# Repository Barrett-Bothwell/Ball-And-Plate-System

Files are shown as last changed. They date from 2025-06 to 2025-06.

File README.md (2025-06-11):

# Ball and Plate Control System

Watch the demo video (https://www.youtube.com/watch?v=V8rTU_FPlsE)

*Click the image above to watch a demo of the system in action!*

A dynamic balancing system that uses an **ESP32-C3 Super Mini**, **MG995 servos**, and a **resistive touchscreen** to control the position of a ball on a plate. The system implements **modern control theory** for real-time position stabilization and uses **6302view** for visualization and debugging.
By Barrett Bothwell and Kolby Kriegelstein

---

## Features

- Real-time ball position control using state-space or observer-based feedback
- Circular pattern sert point option
- Input via resistive touchscreen for ball position sensing
- Output actuation using MG995 servos
- Visualization with **6302view**
- Built on the ESP32-C3 Super Mini platform

---

## Components Used

| Component | Description |
|---|---|
| ESP32-C3 Super Mini | Microcontroller for control and I/O |
| MG995 Servos (x2) | Control pitch and roll of the plate |
| M2x65mm Linkage Rod | Linkage Rod used to connect the plate to the servo motors |
| M2 Metal Clevis | Clevis used to connect the rod to the servo and top plate |
| Universal Joint Coupler | 10mm inner diameter universal joint |
| 7/8" Stainless Steel Ball | Ideal ball size for system and plate |
| 4-Wire Resistive Touchscreen | Senses ball position (165mm by 100mm)  
| 6302view | PC-based visualization & tuning tool |
| 5v Power Supply | Stable 5V source for servos and ESP32 |

---

## Wiring Setup

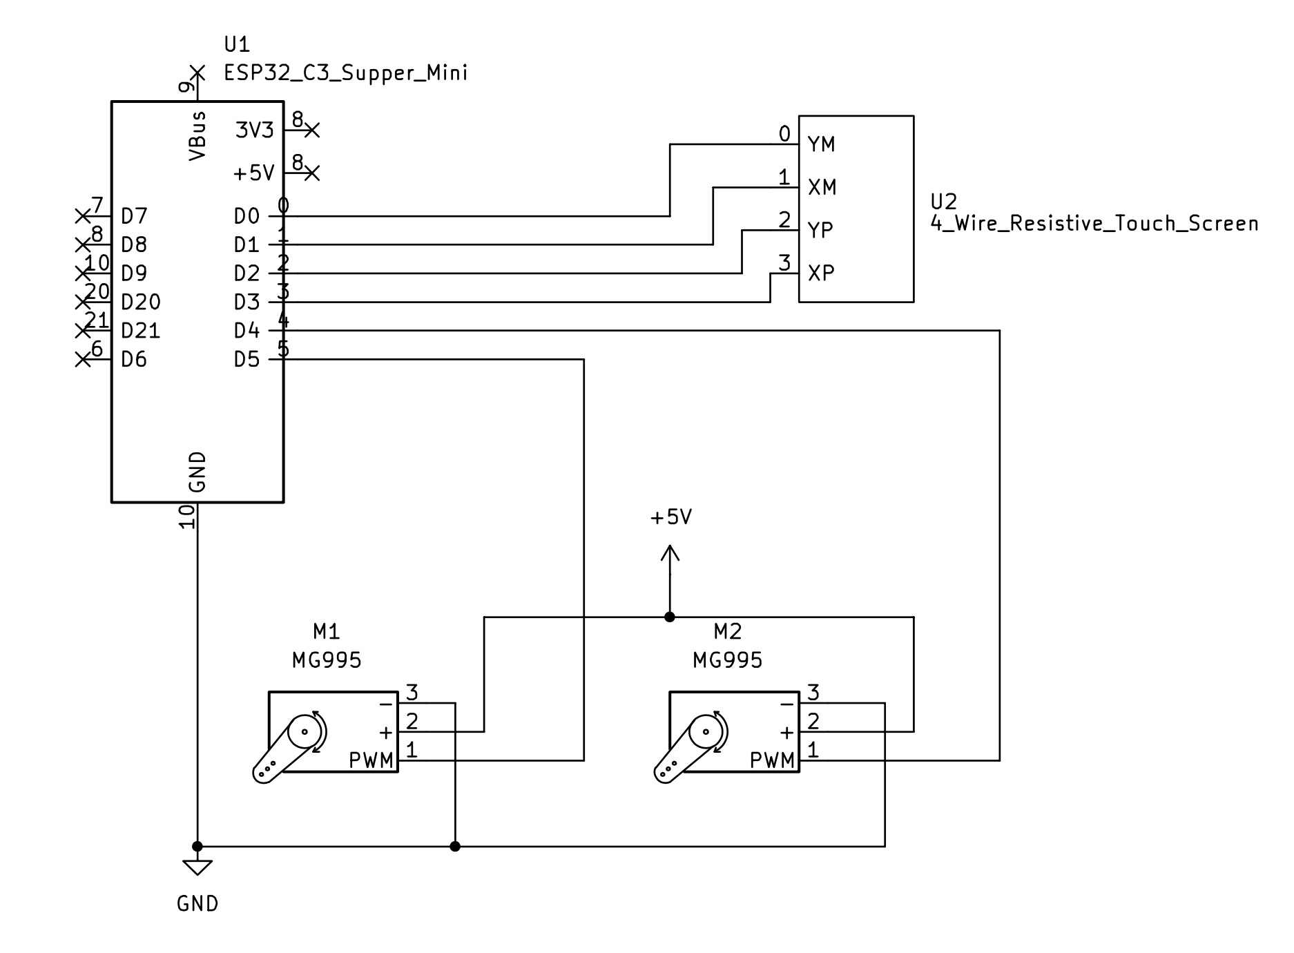
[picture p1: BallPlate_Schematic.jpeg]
Ball and Plate Schematic


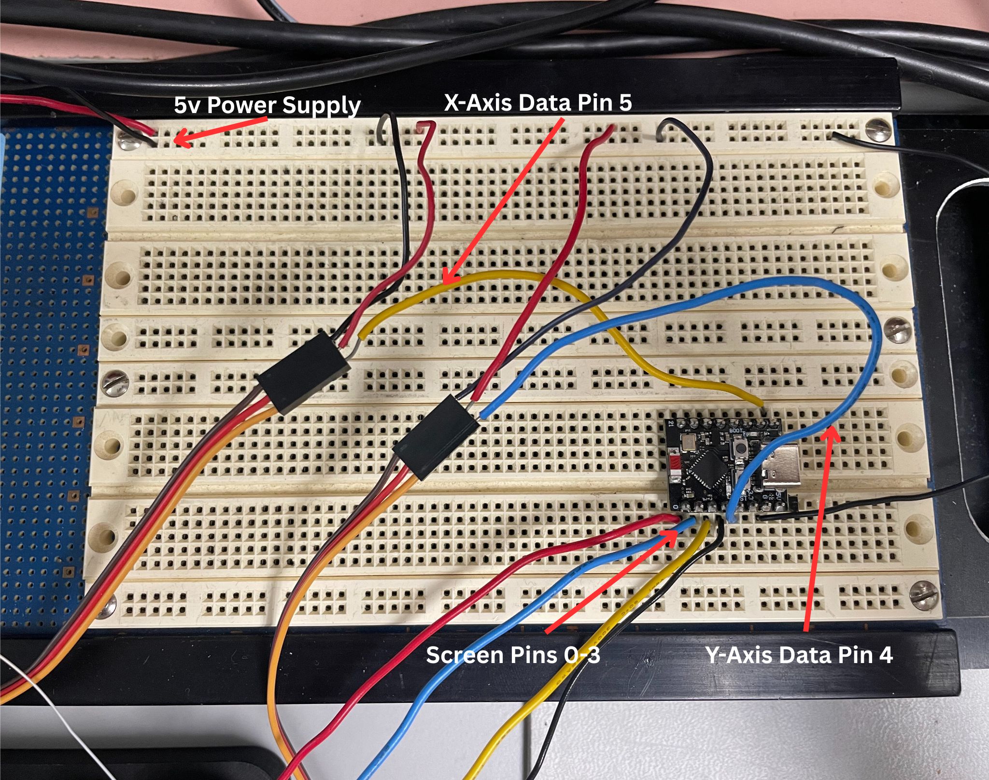
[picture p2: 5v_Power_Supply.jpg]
Wiring Diagram


| ESP32-C3 Pin | Connection |
| --- | --- |
| 5V | Servo power supply, can use external power supply |
| GND | Common ground for all components |
| Pin 5 | Servo X PWM signal |
| Pin 4 | Servo Y PWM signal |
| Pin 0 | Touchscreen X+ (analog read) |
| Pin 2 | Touchscreen X- (output control)  |
| Pin 3 | Touchscreen Y+ (output control)  |
| Pin 1 | Touchscreen Y- (analog read) |

---

## Setup Instructions

Follow these steps to set up the Ball and Plate Control System:

1. **Hardware Assembly**:
   - Start by 3D printing the top tray and bottom base
   - Once printed mount the motors by screwing them into the two posts
   - Connect the top tray and bottom base together using the universal joint
   - Finally use the metal clevises and linkage rods to connect the motors to the top tray
   - Wire the components as per the wiring diagram provided in the **Wiring Setup** section.

2. **Software Setup**:
   - Install the required development environment for the ESP32-C3 (e.g., [PlatformIO](https://platformio.org/) or Arduino IDE).
   - Open the project in your development environment and upload the firmware to the ESP32-C3.

3. **6302view Setup**:
   - Download and install **6302view** from its [GitHub repository](https://github.com/almonds0166/6302view).
   - Connect the ESP32-C3 to your PC via USB or Wi-Fi.
   - Run **6302view** and configure the serial or Wi-Fi connection to the ESP32-C3.
   - Use the offset sliders in **6302view** to level the plate if necessary.

5. **Testing**:
   - Power on the system and ensure all components are functioning correctly.
   - Use **6302view** to monitor the ball position and adjust the control parameters as needed.

---

## 6302view Integration

- **Purpose**: Enables real-time monitoring and set point placement of the system over serial communication.

- **Visualized Parameters**:
  - Current ball position (X, Y)
  - Currently commented out servo command plots
  - Target/reference position slider
  - Axis Offset sliders to account for uneven surfaces
  - Circle toggle to target a circular pattern for the ball

---

## Control Theory

This project uses a **state-space feedback controller** designed using modern control theory. The first step in finding our state space model was deriving the equation using Newton's Laws.

**Deriving the Equations of Motion Using Newton's Laws**:

The first step in designing the control system is to derive the equations of motion for the Ball and Plate system. This is done using Newton's Second Law:
\
F = ma and M = Iα

#### Assumptions:
- The ball rolls without slipping on the plate.
- The plate's motion is limited to small angular displacements (linearization assumption).
- Constant gravitational force acts on the ball.
- No additional rotation on the ball.
- No unwanted movement in the plate.

#### Steps:
1. **Free Body Diagram**:
   - Consider the forces acting on the ball:
     - Gravitational force \(mg\) acting downward.
     - Normal force \(N\) from the plate.
     - Frictional force \(F<sub>f</sub>\) preventing slipping.

2. **Equations of Motion**:
   - For the ball in the x-direction:
     \
     F<sub>f</sub> - w sin(θ) = -ma
     
   - For the rotation of the ball:
   \
    F<sub>f</sub>R = Iα 

3. **Combine Equations**:
   - Substitute the torque equation into the force equations to eliminate F<sub>f</sub>.
   \
    R(w sin(θ) - ma) = Iα

4. **Simplify**:
   - By plugging in the moment of inertia for a solid sphere:
   \
    I = 2/5mR^2
   
   - With additional algebraic simplification and a small angle approximation of sin we get:
   \
   a = 5/7gθ

This equation describes the behavior of the ball for both the respective x and y accelerations in terms of the plate angle θ. These equations will now be used to construct the state-space representation of the system.

**State Space Representation**

The state-space representation of a system is given by:
\
$\dot{x}$ = Ax + Bu

y = Cx + Du

Where:
- \( x \) is the **state vector** (e.g., ball position and velocity).
- \( u \) is the **input vector** (e.g., plate angles).
- \( y \) is the **output vector** (e.g., ball position and velocity).
- \( A, B, C, D \) are the system matrices.

#### Steps:

1. Define the States
For the Ball and Plate system, the states can be defined as:
- x = Ball position in the x-direction
- $\dot{x}$  = Ball velocity in the x-direction
- y = Ball position in the y-direction
- $\dot{y}$ = Ball velocity in the y-direction

2. Inputs and Outputs
- **Inputs \( u \)**: Plate angles in the x and y directions

- **Outputs (\( y \))**: Ball positions in the x and y directions

3. Derive the State Equations
Using the linearized equations of motion:
\[
a<sub>x</sub> =  5/7gθₓ, a<sub>y</sub> = 5/7gθᵧ
\]
We can write the second-order equations for the ball’s motion:
\[
$\dot{x}$ = 5/7gθₓ, $\dot{y}$ = 5/7gθᵧ
\]

4. Write in Matrix Form
Combine the equations into matrix form to find the final state space model:

\
$\dot{x}$ = Ax + Bu
\
y = Cx + Du

Where:

A = \
    [ 0 ,  1 ,  0 ,  0 ]\
    [ 0 ,  0 ,  0 ,  0 ]\
    [ 0 ,  0 ,  0 ,  1 ]\
    [ 0 ,  0 ,  0 ,  0 ]

B = \
    [   0 ,       0   ]\
    [ 5/7*g ,     0   ]\
    [   0 ,       0   ]\
    [   0 ,   5/7*g  ]

C = \
    [ 1 ,  0 , 0 , 0 ]\
    [ 0 , 1 , 0 , 0 ]\
    [ 0 , 0 , 1 , 0 ]\
    [ 0 , 0 , 0 , 1 ]

D = \
    [ 0 , 0 , 0 , 0 ]\
    [ 0 , 0 , 0 , 0 ]\
    [ 0 , 0 , 0 , 0 ]\
    [ 0 , 0 , 0 , 0 ]

Now that our A, B, C, and D matrices are defined we must find the discrete versions of each. For our application the discrete version of the C and D matrix are the same and the A and B matrix are:

A<sub>d</sub> = \
    [ 1  ,  0.02 , 0  ,  0    ]\
    [ 0  ,  1  ,   0  ,  0    ]\
    [ 0  ,  0   ,  1  ,  0.02 ]\
    [ 0 ,   0  ,   0  ,  1    ]

B<sub>d</sub> = \
    [   0   ,    0   ]\
    [ 5/7*g  ,   0   ]\
    [   0    ,   0   ]\
    [   0  ,  5/7*g  ]

**Pole Placement**

Now that we have our state space model we can use eigenvlue pole placement in order to find our gain matrices. This was done using the python control package with our desired eigenvalues. These gain matrices were used for the simulation, but further tuning was needed for the physical system. The theoretical gain matrices were:

K = \
    [ 0.12 , 0.02 , 0 , 0 ]\
    [ 0 , 0.12 , 0 , 0 ]\
    [ 0 , 0 , 0.1 , 0.02 ]\
    [ 0 , 0 , 0 , 0.1 ]

G =\
    [0.3568 , 0.4959 , 0 , 0]\
    [0 , 0 , 0.3568 , 0.4959]

The G matrix is the gain matrix which needed additional tuning. The K matrix is the observer gain matrix and did not need additional tuning.

**Observer**

We chose to use a discrete observer in order to smooth out some of the noise from our position readings and velocity approximations. We will achieve this by using the equation for a discrete observer:

x̂ = A<sub>d</sub> x̂ + B<sub>d</sub> u + K (y - C x̂)

Where x̂ is the approximated values for position and velocity in both the x and y axes.

**Feedback Control**

Now that we have our state-space model and gain matrices we can apply feedback to our system. We will accomplish this by finding the difference between our setpoint positions and velocities and the observer state. We will then multiply this difference by our G matrix to solve for u.

---

## Potential Improvements

- **Hardware Improvements**
  - The 3D printed structure had some minor warping on the top piece
    - Modifications to the CAD model could be made to reduce this warping
    - Printing procedure could change to modify this as well
  - Cheap servos were used which although they had enough power and range of motion the clarity is low
    - Higher quality, more accurate servos could be used to ensure the desired angle is output
    - 3 or more servos could have been used in a different arrangement to produce more accurate plate angle outputs

- **Software Improvements**
  - Both G and K matrices can be fine-tuned to ensure optimal convergence
  - Additional plots can be added using 6302 view
    - Currently code for angles is commented out
    - Observer state plots could be added

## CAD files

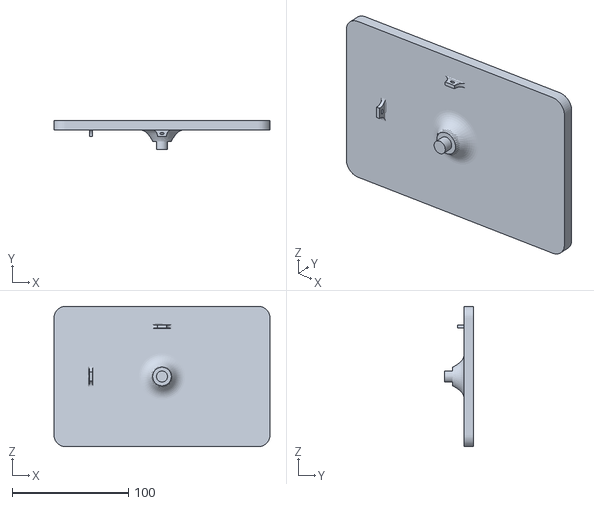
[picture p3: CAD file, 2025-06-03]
3D_Model_Files/Top_Tray.STL
185.5 x 25.0 x 120.5

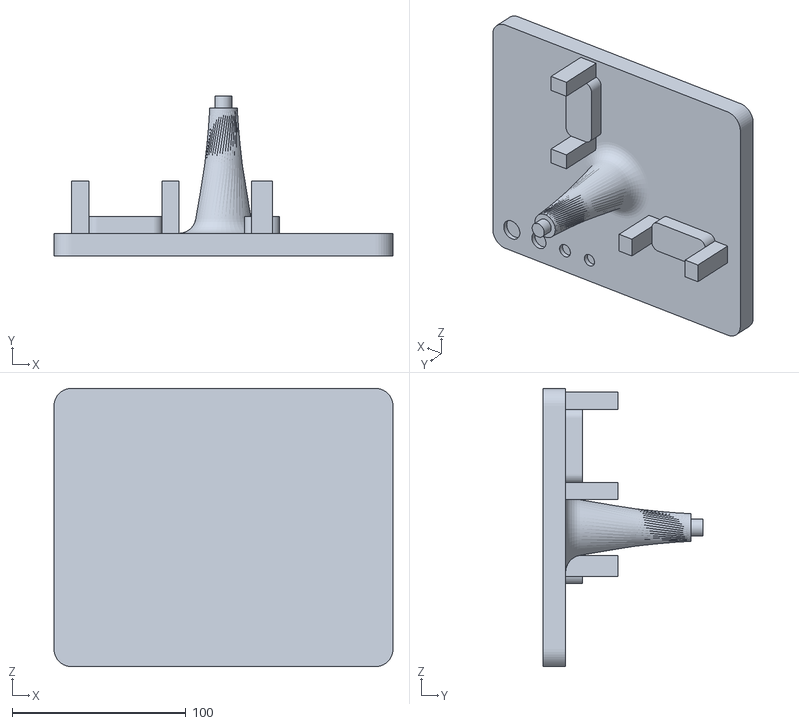
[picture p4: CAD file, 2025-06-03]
3D_Model_Files/Bottom_Base.STL
195.0 x 92.0 x 160.0

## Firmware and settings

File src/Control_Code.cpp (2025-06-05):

#include <Arduino.h>
#include <Six302.h>
#include <BasicLinearAlgebra.h>
#include <stdint.h>
#include <TouchScreen.h>
#include <ESP32Servo.h>

//Touchscreen Pin Definitions
#define YP 2  // must be an analog pin, use "An" notation!
#define XM 1  // must be an analog pin, use "An" notation!
#define YM 0   // can be a digital pin
#define XP 3   // can be a digital pin


// These values are in microseconds
#define STEP_TIME 10000 // (0.01s)
#define REPORT_TIME 100000 // (second)

CommManager cm(STEP_TIME, REPORT_TIME);

float T = STEP_TIME / 1000000.0; // Convert to seconds

//Initialization of variables
float prev_x = 0;
float prev_y = 0;
float x_meas = 0;
float y_meas = 0;
float x_dot = 0;
float y_dot = 0;
float raw_x = 0;
float phi_x = 0;
float phi_y = 0;
float x_offset = -2.8;
float y_offset = -2.8;
float theta_x = 0;
float theta_y = 0;
float x_setpoint = 100; 
float y_setpoint = -150;
bool circle = false; // Circle mode toggle
float radius = 25;

//TouchScreen Setup
TouchScreen ts = TouchScreen(XP, YP, XM, YM, 300);

unsigned long lastTouchTime = 0; // Timestamp of the last valid touchscreen press
const unsigned long TOUCH_TIMEOUT = 500000; // Timeout period in microseconds (0.5 seconds)

#define TS_MINX -3072  // calibrated minimum X value
#define TS_MAXX 420  // calibrated maximum X value
#define TS_MINY -2500  // calibrated minimum Y value
#define TS_MAXY 350  // calibrated maximum Y value

//Servo Setup
Servo servox;
Servo servoy;
int minUs = 500; // Minimum pulse width in microseconds
int maxUs = 2500; // Maximum pulse width in microseconds

int servoxPin = 5;
int servoyPin = 4;

//Define Necessary Matrices
BLA::Matrix<4, 4> A = {
  0, 1, 0, 0,
  0, 0, 0, 0,
  0, 0, 0, 1,
  0, 0, 0, 0
};

BLA::Matrix<4, 2> B = {
  0, 0,
  5.0/7.0*9.81, 0,
  0, 0,
  0, 5.0/7.0*9.81
};

BLA::Matrix<4, 4> C = {
  1, 0, 0, 0,
  0, 1, 0, 0,
  0,0,1,0,
  0,0,0,1
};

BLA::Matrix<4, 2> D = {
  0, 0,
  0, 0,
  0, 0,
  0, 0
};

BLA::Matrix<4, 4> K = {
  0.12, 0.02, 0, 0,
  0, 0.12, 0, 0,
  0, 0, 0.1, 0.02,
  0, 0, 0, 0.1
}; // Observer gain matrix (tune this based on your system)

BLA :: Matrix<2,4> G = {
  0.3568 / 500, 0.4959 / 600, 0, 0, 
  0, 0, 0.3568 / 500 * 2.63/3.75, 0.4959 / 550 * 2.63/3.75
}; // Control gain matrix (500 xpos, 850 xvel, 500 ypos, 550 yvel) 
//these denominators will be less sensitive and work better for the circle mode

// State and observer variables
BLA::Matrix<4> x_hat = {0, 0, 0, 0}; // Initial estimated state
BLA::Matrix<4> y = {0, 0, 0, 0};           // Measured output
BLA::Matrix<2> u = {0, 0};           // Control input
BLA::Matrix<4> error = {0, 0, 0, 0}; // Error between estimated and actual state
BLA::Matrix<4> setpoint = {x_setpoint, 0, y_setpoint, 0}; // Example: stationary at origin

// Discrete-time matrices A_d and B_d Found using Simulation.py
BLA::Matrix<4, 4> A_d = {
    1, 0.02, 0, 0,
    0, 1, 0, 0,
    0, 0, 1, 0.02,
    0, 0, 0, 1
};

BLA::Matrix<4, 2> B_d = {
    0.00140143, 0,
    0.14014286, 0,
    0, 0.00140143,
    0, 0.14014286
};

void setup() {
  //6302 ViewSetup
  cm.addPlot(&x_meas, "X Position", -100, 100);
  // optional to plot phi_x on 6302 view
  //cm.addPlot(&phi_x, "phi_x", 33, 57);
  cm.addPlot(&y_meas, "Y Position", -100, 100);
  //option to plot phi_y on 6302 view
  //cm.addPlot(&phi_y, "phi_y", 33, 57);
  //Optional to plot x_dot and y_dot on 6302 view 
  //cm.addPlot(&x_dot, "X Velocity", -150, 150);
  //cm.addPlot(&y_dot, "Y Velocity", -150, 150);
  

  // Add sliders for setpoint adjustment
  cm.addSlider(&x_setpoint, "X Setpoint", 0, 165, 50, 1);
  cm.addSlider(&y_setpoint, "Y Setpoint", -180, -100, -120, 1);
  cm.addSlider(&x_offset, "X Offset", -5, 5, -3.75, 1);
  cm.addSlider(&y_offset, "Y Offset", -5, 5, -2.5, 1);
  cm.addToggle(&circle, "Circle");

  //Servo Setup Code
    servox.attach(servoxPin, minUs, maxUs);
    servoy.attach(servoyPin, minUs, maxUs);

  // Allow allocation of all timers
	ESP32PWM::allocateTimer(0);
	ESP32PWM::allocateTimer(1);
	ESP32PWM::allocateTimer(2);
	ESP32PWM::allocateTimer(3);

  cm.connect(&Serial, 115200);
}
void loop() {
  static unsigned long lastTime = 0; // Store the timestamp of the previous loop iteration
  unsigned long currentTime = micros(); // Get the current time in microseconds

  // Calculate the actual time step (T) in seconds
  float T = (currentTime - lastTime) / 1000000.0; // Convert microseconds to seconds
  lastTime = currentTime; // Update the last time for the next iteration

   // 1. Read position from resistive touchscreen
   TSPoint p = ts.getPoint();
 
   if (p.x == -3072 || p.y == 1023) {
     // Valid touchscreen press detected
     x_meas = prev_x;
     y_meas = prev_y;

   } else {
     // Use the last valid measurement
     x_meas = map(p.x, TS_MINX, TS_MAXX, -82.5, 82.5);
     y_meas = map(p.y, TS_MINY, TS_MAXY, -50, 50);
     lastTouchTime = currentTime; // Update the last touch timestamp
   }

  // 2. Estimate velocity
  x_dot = (x_meas - prev_x) / T;
  y_dot = (y_meas - prev_y) / T;
  prev_x = x_meas;
  prev_y = y_meas;

  // 3. Update state vector
  BLA::Matrix<4> y = {x_meas, x_dot, y_meas, y_dot};

  // 4. Define the setpoint (desired state)
  if (circle) {
    // Circle mode: Setpoint follows a circular path
    float time = currentTime / 1000000.0; // Convert to seconds
    setpoint = {radius*cos(time)+x_setpoint,-radius*sin(time) ,radius*sin(time)+y_setpoint ,radius*cos(time) };

  } else {
    setpoint = {x_setpoint, 0, y_setpoint, 0};
  }

  // Update Observer State
  x_hat = A_d * x_hat + B_d * u + K * (y - C * x_hat);

  BLA::Matrix<4> error = x_hat - setpoint; // Compute error
  
  u = -G * error;

  // 7. Convert control input to degrees
  theta_x = u(0) * 180 / PI; // Convert u(0) to degrees
  theta_y = u(1) * 180 / PI; // Convert u(1) to degrees

  phi_x = (theta_x + 45); // Convert to servo angle 
  phi_y = (theta_y + 45); // Convert to servo angle

  phi_x = constrain(phi_x, 38, 57) - x_offset; // Constrain phi_x to ensure system doesnt break
  phi_y = constrain(phi_y, 34, 51) - y_offset; // the offset values are used to adjust for uneven tables

  // Send phi_x and phi_y to servos
  servox.write(phi_x); // 45 degrees is approximately zero for x
  servoy.write(phi_y); // 45 degrees is approximately zero for y

  cm.step();
}

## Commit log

2025-05-28 Initial commit of Ball and Plate System using 6302view
    git push -u origin main
    git push -u origin main
    git push -u origin main
    git push -u origin main
    .git/REBASE_EDITMSGgit push -u origin main
2025-05-28 Initial commit of Ball and Plate System using 6302view
2025-06-03 Added 3D model files and modified the README
    [Bottom_Base.STL, Top_Tray.STL]
2025-06-05 Added Schematic
